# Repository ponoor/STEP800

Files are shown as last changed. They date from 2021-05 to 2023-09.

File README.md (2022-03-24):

# STEP800
8-axis stepper motor driver for Open Sound Control

step800_r1_1

STEP800 is a 8-axis stepper motor driver designed for art or design projects. STEP800 combines the following elements into one single board:

- [Arduino Zero](https://www.arduino.cc/en/Guide/ArduinoZero)
- Ethernet shield
- 8 stepper motor drivers
- Sensor inputs for homing

The current firmware is focused on working with [Open Sound Control](http://opensoundcontrol.org/) (OSC) via Ethernet, which is a common protocol for creative coding environments, like openFrameworks, Processing, Max, Unity, or Touch Designer.

Stepper driver chips are STMicroelectronics's [L6470](https://www.st.com/en/motor-drivers/l6470.html) which provide most of functionalities as a stepper driver.

Friend of STEP800 : [STEP400](https://github.com/ponoor/STEP400)

## Store
https://ponoor.com/en/shop/

## Documentation
https://ponoor.com/en/docs/step-series/

Forum: https://github.com/ponoor/step-series-support/discussions

## Repository Contents
### Firmware

**Important Note:**
The latest firmware is available at [STEP-series Universal Firmware](https://github.com/ponoor/step-series-universal-firmware) repository. Following directories and Releases are not maintained anymore. 

These 2 folders contain same codes.
- [/STEP800_firmware](https://github.com/ponoor/STEP800/tree/main/STEP800_firmware) : Arduino Sketch folder
- [/firmware-platformIO/STEP800_firmware](https://github.com/ponoor/STEP800/tree/main/firmware-platformIO/STEP800_firmware) : PlatformIO folder

### Hardware
[/hardware](https://github.com/ponoor/STEP800/tree/main/hardware) : Eagle design files, BOM lists, and a schematics PDF

### Others
[/configTool](https://github.com/ponoor/STEP800/tree/main/configTool) : The configuration tool consists of a html and JavaScritpts.

## Firmware dependency
- **[OSC Library](https://github.com/CNMAT/OSC)** from CNMAT
- **[Ponoor L6470 Library](https://github.com/ponoor/Ponoor_L6470_Library)**
- **[ArduinoJSON Library](https://arduinojson.org/)**
- **[Adafruit SleepyDog Arduino Library](https://github.com/adafruit/Adafruit_SleepyDog)**

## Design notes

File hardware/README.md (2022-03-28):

# Diagram
```mermaid
flowchart LR
	MCU ---|SPI/SERCOM4| W5500 --- Ethernet
	MCU --- |SPI/SERCOM3|L6470 --> Motor
  MCU --> |SPI/SERCOM2|74HC165 --> 74HC595 --> MCU
	HomeSw -->|SW| L6470
	DIPSW --> 74HC165
	74HC595 --> Brake
  ```
  
  Check the [document](https://ponoor.com/en/docs/step-series/technical-information/hardware-step800/) for details.

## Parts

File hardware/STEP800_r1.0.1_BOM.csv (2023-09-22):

# | Name | Value | Description | Package | Manufacture | MPN | Qty | Parts | Type | SMT | THT | BGA/QFP
1 | SMD-LED | GREEN | Various green LEDs | LED-0603 | Everlight Elec | 19-213/GHC-YR1S2M/3T | 9 | 3.3V, BUSY1, BUSY2, BUSY3, BUSY4, BUSY5, BUSY6, BUSY7, BUSY8 | SMT | 9
2 | MLCC | 100nF / 25V | 100nF / 20% / 25V / X5R | C0402 | Samsung Electro-Mechanics | CL05A104KA5NNNC | 32 | C1, C3, C7, C8, C9, C10, C12, C13, C14, C15, C16, C17, C20, C21, C24, C31, C32, C33, C34, C35, C44, C45, C46, C47, C72, C73, C74, C75, C84, C85, C86, C87 | SMT | 32
3 | MLCC | 10uF/10V | 10uF / 20% / 10V / X5R | C0805 | Samsung Electro-Mechanics | CL21A106KOQNNNG | 9 | C11, C36, C37, C38, C39, C76, C77, C78, C79 | SMT | 9
4 | MLCC | 47uF/6.3V | 47uF / 20% / 6.3V / X5R | C1206 | Samsung Electro-Mechanics | CL31A476MQHNNNE | 2 | C18, C19 | SMT | 2
5 | MLCC | 10uF/50V | 10uF / 20% / 50V / X5R | C1206 | Samsung Electro-Mechanics | CL31A106KBHNNNE | 2 | C2, C6 | SMT | 2
6 | MLCC | 4.7uF / 6.3V | 4.7uF / 20% / 6.3V / X5R | C0603 | Samsung Electro-Mechanics | CL10A475KQ8NNNC | 1 | C22 | SMT | 1
7 | MLCC | 10nF/50V | 10nF / 20% / 50V / X5R | C0603 | Samsung Electro-Mechanics | CL10B103KB8NNNC | 10 | C23, C28, C40, C41, C42, C43, C80, C81, C82, C83 | SMT | 10
8 | MLCC | 22nF 50V | 22nF / 20% / 50V / X5R | C0402 | Walsin Tech Corp | 0402F223Z500CT | 1 | C27 | SMT | 1
9 | MLCC | 6.8nF/25V | 6.8nF / 20% / 25V / X5R | C0402 | Murata Electronics | GCM155R71E682KA37D | 2 | C29, C30 | SMT | 2
10 | MLCC | 22pF/50V | 22pF / 10% / 50V / X5R | C0402 | YAGEO | CC0402JRNPO9BN220 | 4 | C4, C5, C25, C26 | SMT | 4
11 | MLCC | 220nF / 25V | 220nF / 20% / 25V / X5R | C0603 | Samsung Electro-Mechanics | CL10F224ZA8NNNC | 8 | C65, C67, C69, C71, C105, C107, C109, C111 | SMT | 8
12 | Chemical Capacitor | 220uF / 50V | 220uF �}20% 50V 10mm | SMD,10x10mm | Rubycon | 50TZV220M10X10.5 | 8 | C48, C49, C50, C51, C88, C89, C90, C91 | SMT | 8
13 | MLCC | 100nF/50V | 100nF / 20% / 50V / X5R | C0603 | Walsin Tech Corp | 0603B104K500CT | 32 | C52, C53, C54, C55, C56, C57, C58, C59, C60, C61, C62, C63, C64, C66, C68, C70, C92, C93, C94, C95, C96, C97, C98, C99, C100, C101, C102, C103, C104, C106, C108, C110 | SMT | 32
14 | Shrouded header | 2.5mm, 4P | B4B-XASK-1 | B4B-XASK-1 | JST | B04B-XASK-1(LF)(SN) | 8 | CN1, CN2, CN3, CN4, CN9, CN10, CN11, CN12 | NO MOUNT
15 | Shrouded header | 2.5mm, 3P | B3B-XASK-1 | B3B-XASK-1 | JST | B03B-XASK-1(LF)(SN) | 8 | CN5, CN6, CN7, CN8, CN13, CN14, CN15, CN16 | THT | 8
16 | Switching diode array | BAV99 | Series-pair diode array | SOT23-3 | Nexperia | BAV99,215 | 8 | D14, D15, D16, D17, D26, D27, D28, D29 | SMT | 8
17 | Zener Diode | 5.6V, 300mW | 5.6V �}7% 300mW | SOD-323 | CBI | MM3Z5V6 | 1 | D4 | SMT | 1
18 | SMD-LED | Red | general LED red | LED-0603 | Lite-On | LTST-C193KRKT-5A | 9 | FLAG1, FLAG2, FLAG3, FLAG4, FLAG5, FLAG6, FLAG7, FLAG8, TX | SMT | 9
19 | Ethernet Controller |  |  | TQFP48 | WIZnet | W5500 | 1 | IC1 | SMT | 1 |  | 1
20 | DIP Switch |  | 8 digits | 2.54mm pitch SMD | kangshen | DSIC08LSGET | 1 | ID | SMT | 1
21 | DC Power receptacle |  | DC Power Receptacle Jack 5A 2.0mm 6.2mm | POWERJACK_SLOT | XKB Connectivity | DC-005-5A-2.0 | 1 | J1 | THT |  | 1
22 | Box header |  | Header 10P 0.100"(2.54mm) 2 | 61201021621 | BOOMELE(Boom Precision Elec) | C5665 | 1 | J2 | THT |  | 1
23 | Micro SD card slot |  |  |  | XUNPU | TF-115K | 1 | J4 | SMT | 1
24 | 3.81mm 4pin header |  |  |  | Ningbo Kangnex Elec | WJ15EDGVC-3.81-4P | 8 | J5, J6, J7, J8, J9, J10, J11, J12 | THT |  | 8
25 | SMD-LED | Orange | general LED orange | LED-0603 | Lite-On | LTST-C191KFKT | 1 | L | SMT | 1
26 | Ferrite Beads | 330R-1500MA | 330ƒ¶ @ 100MHz 1.5A | L0805 | Murata Electronics | BLM21PG331SN1D | 2 | L1, L2 | SMT | 2
27 | DC-DC Converter | P78E05-1000 | 9-36V input, 5V output, 1000mA | CONV_P78E05-1000 | CUI Inc. | P78E05-1000 | 1 | PS1 | THT |  | 1
28 | P-MOSFET |  | 60V 50A | D-PAK(TO252) | VBsemi Elec | STD35P6LLF6-VB | 1 | Q1 | SMT | 1
29 | Crystal Resonators | 32.768kHz | CRYSTAL | SMD-3215_2P | Seiko | SC-32S32.768kHz20PPM6pF | 1 | Q2 | SMT | 1
30 | Crystal Oscillator |  | 16MHz �}100ppm 3.3V | SMD5032-4P | Shenzhen SCTF Elec | S5D16.000000B20F30T | 1 | Q3 | SMT | 1
31 | Chip Resistor | 5.1k | �}0.5% 0.1W | R0603 | YAGEO | RC0603FR-075K1L | 2 | R1, R2 | SMT | 2
32 | Chip Resistor | 1M 1/10W | 5% 1/10W | R0603 | YAGEO | AC0603JR-071ML | 1 | R10 | SMT | 1
33 | Chip Resistor | 10R | 5% 1/10W | R0603 | YAGEO | RC0603JR-0710RL | 1 | R11 | SMT | 1
34 | Chip Resistor | 330R | 5% 1/10W | R0603 | YAGEO | RC0603JR-07330RL | 3 | R12, R13, R22 | SMT | 3
35 | Chip Resistor | 100R | 5% 1/10W | R0603 | YAGEO | RC0603JR-07100RL | 8 | R14, R15, R16, R17, R18, R19, R20, R21 | SMT | 8
36 | Chip Resistor | 100k | 5% 1/10W | R0603 | YAGEO | RC0603JR-07100KL | 4 | R3, R4, R5, R9 | SMT | 4
37 | Chip Resistor | 12.4K | 1�“ 1/10W | R0603 | YAGEO | AC0603FR-0712K4L | 1 | R8 | SMT | 1
38 | Tactile Switch |  | SWITCH-SPST | 4.6x3.2 | ALPS Electric | SKRPABE010 | 1 | RESET | SMT | 1
39 | Array Chip Resistor | 100k | 5% 1/16W | R0603 x4 | Bourns | CAY16-104J4LF | 2 | RN1, RN2 | SMT | 2
40 | Array Chip Resistor | 330 | 5% 1/16W | R0603 x4 | Bourns | CAY16-331J4LF | 5 | RN3, RN6, RN7, RN8, RN9 | SMT | 5
41 | Array Chip Resistor | 33 | 5% 1/16W | R0603 x4 | Bourns | CAY16-330J4LF | 1 | RN4 | SMT | 1
42 | Array Chip Resistor | 49.9 | 1% 1/16W | R0603 x4 | Bourns | CAY16-49R9F4LF | 1 | RN5 | SMT | 1
43 | SMD-LED | Yellow | general LED yellow | LED-0603 | Lite-On | LTST-C191KSKT | 1 | RX | SMT | 1
44 | Pin Header | 10 pin | Cortex Debug Connector | 1.27mm Pin Header 10P | Amphenol ICC | 20021121-00010C4LF | 1 | SWD | SMT | 1
45 | Logic IC | 74HC165PW | 8-bit parallel-in/serial out shift register | TSSOP16 | Nexperia | 74HC165PW,118 | 1 | U1 | SMT | 1 |  | 1
46 | TVS Diode Array | USBLC6-2SC6 | STMicroelectronics USBLC6 | SOT23-6L | UMW | USBLC6-2SC6 | 1 | U2 | SMT | 1
47 | Logic IC | 74HC595 | 8-Bit Shift Register (Serial to Parallel) | TSSOP16 | Nexperia | 74HC595PW,118 | 1 | U3 | SMT | 1 |  | 1
48 | Voltage Regulator | LD1117S33 | 3.3V 0.8A | SOT223 | STMicroelectronics | LD1117S33TR | 1 | U4 | SMT | 1
49 | MCU |  |  | TQFP-48 | Microchip | ATSAMD21G18A-AU | 1 | U5 | SMT | 1 |  | 1
50 | Stepper Driver IC |  |  | HTSSOP28 | STMicroelectronics | L6470HTR | 8 | U6, U7, U8, U9, U10, U11, U12, U13 | SMT | 8 |  | 8
51 | USB Type C Connector |  | USB - Type C Female 16 SMT | USB-C_USB2.0-TYPE-C | XKB Connectivity | U262-161N-4BVC11 | 1 | USB1 | THT |  | 1
52 | Barrier Terminal Block | 7.62mm, 2P |  | 7.62mm | Ningbo Kangnex Elec | WJ25C-B-7.62-2P | 1 | X1 | THT |  | 1
53 | Crystal Resonators | 25MHz | 25MHz �}20ppm12pF | CRYSTAL-3225 | Yangxing Tech | X322525MOB4SI | 1 | X2 | SMT | 1
54 | RJ45 Jack with Magnetics |  |  |  | Hanrun | HR871181A | 1 | X3 | THT |  | 1
 |  |  |  |  |  |  |  |  |  | 201 | 14 | 12

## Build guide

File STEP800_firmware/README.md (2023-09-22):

<strong>This directory is not up to date, and not maintained any more.</strong>

Please visit STEP-series Universal Firmware repository for the latest firmware.<br />
https://github.com/ponoor/step-series-universal-firmware

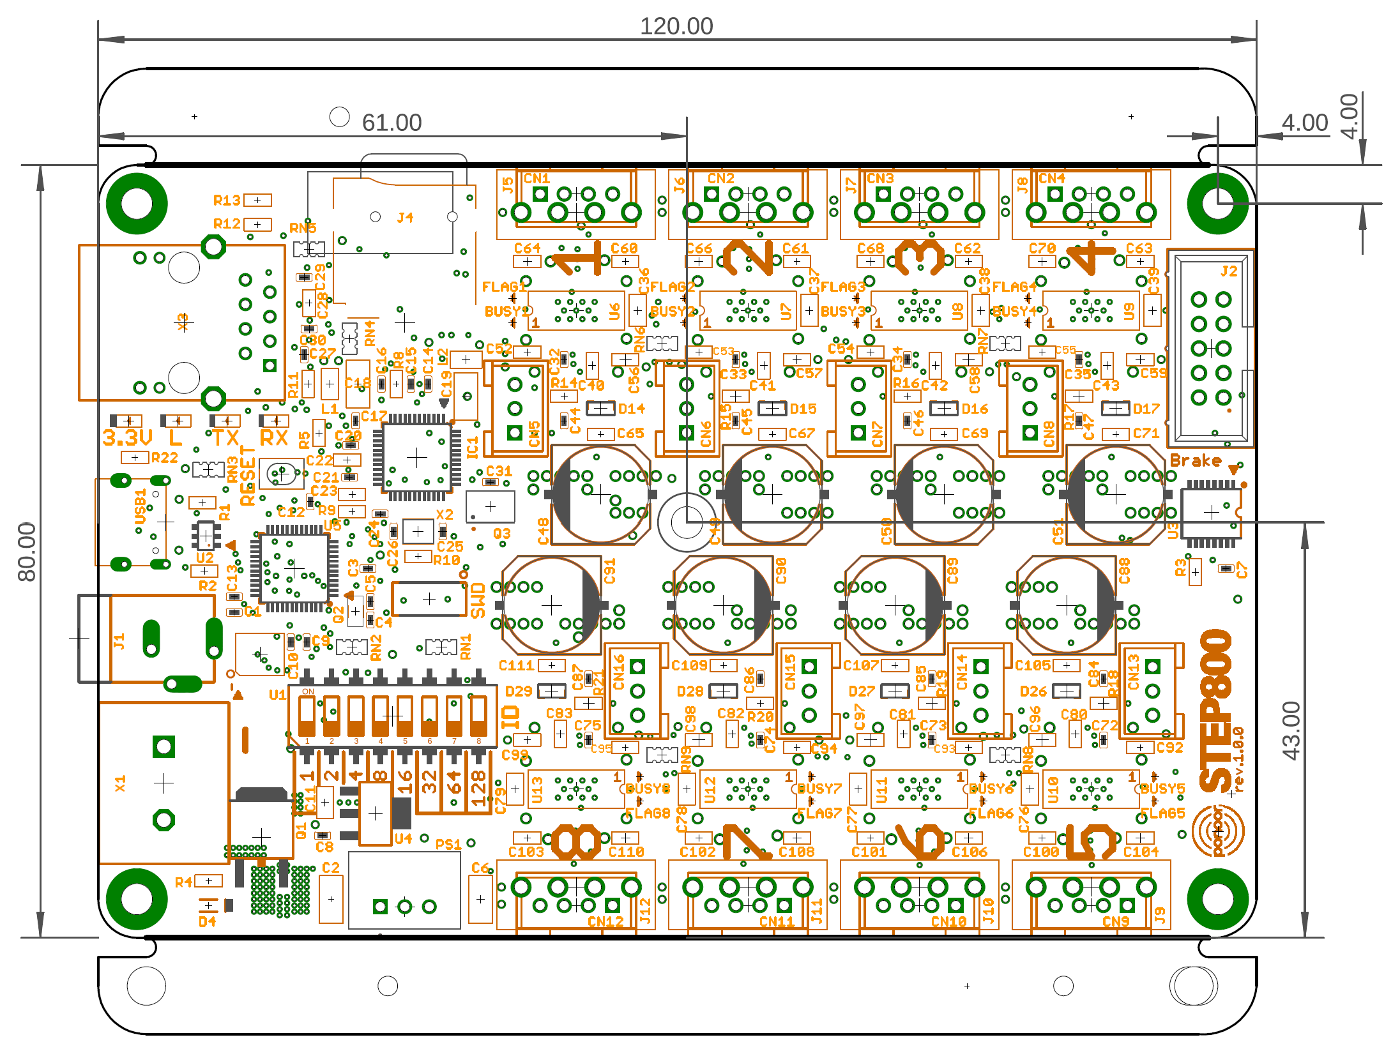
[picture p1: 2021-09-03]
hardware/step800_r1_0_0_dimension.png

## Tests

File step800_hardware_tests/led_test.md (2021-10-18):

# STEP800 LED test
## Preparation
### Connection
- Connect STEP800 to PC with an USB-C to Type-A cable
- Give a 24V power supply to STEP800

### Upload the test program
1. Download the test program from [here](https://github.com/ponoor/STEP800/tree/develop/step800_hardware_tests/step800_led_test), or unizip the attached file. 
2. Open the `step800_led_test.ino` with Arduino IDE.
3. Specify the IDE's target board as Arduino Zero (Native USB Port).


4. Click to the "Tools" menu and then *Port*. Then you should be able to find a serial port(s) and select one with information as `Arduino Zero (Native USB Port))` .


5. Click the upload button. The compile process will take a while.
6. After the compile process is done, Arduino IDE will start upload it to STEP800. You will see the `TX` and `RX` LEDs on STEP800 are blinking during the upload process.
7. If the uploading process is done without problems, you will see the `L` led is turned on.

## Test
### Open the Serial Monitor
Click the lens button on the top right corner of the IDE window.


Then you will see a new Serial Monitor window. You will find some settings in the bottom of the window but you can leave them as defaults.

### FLAG LEDs test
Select a transmission text form (see below) and type `f`  then return key.
This command turn all FLAG LEDs on.


### BUSY LEDs test
Type `b` + return key should cause turning all BUSY LEDs on.

### Clear LEDs
Type `c` + return key will turn all LEDs off.

---

rev 2021-09-13-01, by kanta

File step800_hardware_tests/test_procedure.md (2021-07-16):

## Preparation
### Required tools
- PC which installed Arduino IDE software
- Atmel-ICE Basic https://www.microchip.com/DevelopmentTools/ProductDetails/ATATMEL-ICE
- Power Supply DC jack 24V 1A
- microSD or microSDHC card
- USB Type-C to Type-A cable
- Power Supply 24V 1A, with DC plug 5.5mm outer diameter, 2.1mm inter diameter, center plus
- Network Switch which support 100BASE-TX or faster.
- Ethernet cable CAT5 or higher.

### microSD card setup
1. Format the **microSD** or **microSDHC** card with FAT16 or FAT32.
    Note : microSDXC card will not work.
2. Download the test text data from [here](https://raw.githubusercontent.com/kanta/STEP400_prototype/master/rev4/configTool/sample-setups/SM-42BYG011_24V/config.txt).
3. Copy it to the top directory of the microSD card.
4. Remove the card from a PC and put into the microSD card slot on STEP800.

### Arduino IDE setup
1. Download and install latest Arduino IDE from https://www.arduino.cc/en/Main/Software
2. Install SAMD boards core. Procedure is explained here: https://www.arduino.cc/en/Guide/ArduinoZero
3. Specify the target board as `Arduino Zero (Native USB Port)`.


#### Install Arduino Libraries for the test program

1. Open the IDE and click to the "Sketch" menu and then *Include Library*  > *Manage Libraries*.
2. Type "ponoor" to the search box located on the top right of the window. 


3. You should be able to find "Ponoor L6470 Library". Select it and click the *Install* button.
4. Then install one another library “FlashStorage”. The procedure is same as above.

#### Download and Compile the test program

1. Download the program from [here](https://github.com/ponoor/STEP800/blob/main/step800_hardware_tests/Arduino/step800_hardware_tests/step800_hardware_tests.ino), and open it with the Arduino IDE software.
2. Specify the target board as `Arduino Zero (Native USB Port)` .

3. Press the “VERIFY” button. Then Arduino IDE starts the compile the program (which called “Sketch” in the IDE).



4. If the compiling process is done successfully, you will see a “Done compiling.” sign.


## Programming the MCU
### 1. Apply the power supply
- Apply 24V DC to the PCB with DC input jack (5.5mm outer diameter, 2.1mm inter diameter, center plus). 
[ ] Check the green LED (designator `3.3V` )
### 2. Connect Atmel-ICE Basic
- Connect Atmel-ICE Basic with a PC with USB microB cable.
- Connect the programming cable to the “**SAM**” connector of the Atmel-ICE Basic
- For the cable, use the right connector in the following photo to the Atmel-ICE Basic, and the center connector to the PCB.  We won’t use the left connector.


- Remove the small plastic cover from `SWD` pin header on the PCB. Do not discard this cover, we will put this back to the connector later.
- Then connect a programming socket (the 1.27mm pitch 10pin connector in the middle of the cable) to `SWD` pinheader on the PCB. Be aware of the small circle marking which placed the pin no.1 of the `SWD` connector. The red line of the programming cable indicates the pin no.1 side of the programming header.


- [ ] Green LED on Atmel-ICE Basic should be on.

### 3. Burn Arduino bootloader to the PCB
- Arduino bootloader can write from Arduino IDE. Select `Programmer` item from `Tools` menu,  then select `Atmel-ICE`.
    


- Then select `Burn Bootloader` item of `Tools` menu. 
    


- After programming process,
- [ ] Orange LED on the PCB (designator `L` ) will be fading in & out slowly.

### 4. Put the cover back to the SWD connector
Remove Atmel-ICE-Basic from the PCB and put the black plastic cover back to the SWD connector.

## Upload the test program
### Select a serial port from Arduino IDE
1. Connect the USB connector to a PC with an USB type-C cable. 
2. Open the IDE and click to the "Tools" menu and then *Port.* Then you should be able to find a serial port(s) and select one with information as `Arduino Zero (Native USB Port))` .

3. If there is no serial port in the menu, probably the Arduino Zero bootloader isn’t programmed correctly. 
4. Click the upload button. The compile process will take a while. 
5. After the compile process is done, Arduino IDE will start upload it to STEP800. You will see the `TX` and `RX` LEDs on STEP800 are blinking during the upload process.

## Setups for the test
### Select the serial port again
Once the first sketch is uploaded to STEP800, the name of serial port will change from the original one. Select one with information as `Arduino Zero (Native USB Port))` again.

### Connect the Ethernet connector
Connect the Ethernet connector to a network switch with an Ethernet cable. This is used for check the ethernet link connection is established or not. 

## Test Procedure
Finally we are ready to start the test!

### Open a Serial Monitor
Click the lens button on the top right corner of the IDE window.


Then you will see a new Serial Monitor window. You will find some settings in the bottom of the window but you can leave them as defaults.

### Send a test command
Select a transmission text form (see below) and type `t`  then return key.


## Description of each tests
### microSD card slot

**Description**
This test checks the microSD card slot is working correctly or not.
The successful test result will look like this;

     -------------- SD card -------------- 
    SD card initialize: Ok
    SD_DETECT_PIN: 0 Ok
    
    Test result: Passed

**SD card initialize**
This item checks the connection with microSD card. If this test failed, please check followings;

- The microSD card is inserted
- Using a microSD or a microSDHC card, NOT microSDXC
- The microSD card is formatted with FAT16 or FAT32 formant, NOT exFAT 
- SPI wires for the microSD slot are wired correctly. 

**SD_DETECT_PIN**
This items checks the logical correctness of the microSD card detect pin.

**Related pins**

| MCU pin# | Function |
| --- | --- |
| 13 | microSD SPI CS |
| 19 | microSD SPI MOSI (Shared with W5500) |
| 20 | microSD SPI SCK (Shared with W5500)  |
| 21 | microSD SPI MISO (Shared with W5500) |
| 10 | SD_DETECT_PIN |

### Auxiliary Pins

**Descriptions**
This test checks the auxiliary pad pins which exposed in the bottom side of the PCB.
The successful test result will look like this;

     -------------- Auxiliary Pins --------------
    Auxiliary Pins connection state: Ok
    
    Test result: Passed

This test confirms that each pin is not interfering with each other.

**Related pins**

| MCU pin# | Pad name (in Bottom side) |
| --- | --- |
| 31 | SDA |
| 32 | SCL |
| 22 | D38 |
|12|D9|
|11|D8|
|7|A1|
|15|D1|
|30|D7|

### Ethernet

**Descriptions**
This test the Ethernet controller chip and a physical connection of the network.
The successful test result will look like this;

     -------------- Ethernet --------------
    Ethernet hardware status: 3, -EthernetW5500 Ok
    Ethernet link status: 2 ..Ok
    
    Test result: Passed

**Ethernet hardware status**
This test checks the SPI communication with the Ethernet controller chip W5500 (`IC1`). If this test failed, please check the W5500 chip or wiring.

**Ethernet link status**
This test checks the physical connection of Ethernet. This test wait a few seconds to establish the connection. If the connection couldn’t establish within the waiting period, the test becomes failed. If so, please check the followings;

- Ethernet cable is connected with a network switch.
- Check the RJ45 connector `X3` and related components include; `C34, C35, C36, C37, R14, RN2, RN3`

**Related pins**

| MCU pin# | Function |
| --- | --- |
| 9 | W5500 RESET |
| 27 | W5500 SPI CS |
| 19 | W5500 SPI MOSI (shared with microSD) |
| 20 | W5500 SPI SCK (shared with microSD)  |
| 21 | W5500 SPI MISO (shared with microSD) |

### L6470

**Description**
This test checks the motor driver chip L6470. 
The successful test result will look like this;

```
-------------- L6470 --------------     
L6470 SPI connection: Ok
L6470 ID#1
 STATUS: 0x7E30  Ok
 SW_F: 0 Ok
 BUSY: 0 Ok
L6470 ID#2
 STATUS: 0x7E30  Ok
 SW_F: 0 Ok
 BUSY: 0 Ok
L6470 ID#3
 STATUS: 0x7E30  Ok
 SW_F: 0 Ok
 BUSY: 0 Ok
L6470 ID#4
 STATUS: 0x7E30  Ok
 SW_F: 0 Ok
 BUSY: 0 Ok
L6470 ID#5
 STATUS: 0x7E30  Ok
 SW_F: 0 Ok
 BUSY: 0 Ok
L6470 ID#6
 STATUS: 0x7E30  Ok
 SW_F: 0 Ok
 BUSY: 0 Ok
L6470 ID#7
 STATUS: 0x7E30  Ok
 SW_F: 0 Ok
 BUSY: 0 Ok
L6470 ID#8
 STATUS: 0x7E30  Ok
 SW_F: 0 Ok
 BUSY: 0 Ok

Test result: Passed
```

**L6470 SPI connection**
This results shows the physical connection of the SPI daisy chain of 8 L6470s are working or not. All SPI pins of all L6470s and the MCU have to be connected properly to establish the SPI communication.
If this test failed, please check the connections of following pins;

| MCU pin# | L6470 pin# | Function |
| --- | --- | --- |
| 3 | 23 | L6470 SPI CS |
| 8 | 3 | L6470 RESET |
| 25 | 20 | L6470 SPI MOSI |
| 28 | 19 | L6470 SPI SCK  |
| 29 | 18 | L6470 SPI MISO |

**STATUS**
This item shows the status of each PowerSTEP01. There are several possible errors here.

- `OCD(Over Current) detected.` : This error indicates an overcurrent detection event. Probably something is wrong in following pins;

| L6470 pin# | Function |
| --- | --- |
| 1 | OUT1A |
| 14 | OUT1B |
| 15 | OUT2A |
| 28 | OUT2B |

- `UVLO(Under Voltage Lock Out) detected.`  : This error will happen then a VCC of the L6470 is too low.  Check the power supply is connected properly, and following pin connections;

| L6470 pin# | Function |
| --- | --- |
| 2, 26 | VSA |
| 12, 16 | VSB |
| 10 | CP |
| 11 | VBOOT |

- `OCD+UVLO detected.` : This error happens when the external clock source is not provided. Check the crystal oscillator `Q3` and external clock input and output pins of L6470. The external clock is daisy chained among L6470s, `Q3` → `U6` → `U7` → `U8` → `U9` → `U10` → `U11` → `U12` → `U13`.

| L6470 pin# | Function |
| --- | --- |
| 7 | OSCIN |
| 8 | OSCOUT |

**SW_F**
This item checks the state of SW pin of PowerSTEP01, which connected to HOME sensor connector. 

| L6470 pin# | Function |
| --- | --- |
| 4 | SW |

### DIP Switch

**Descriptions**
This test checks the DIP switch (designator `ID`) and you need to move all digits of the switch by yourself to complete the test.
Initially you will see the following message.

```
-------------- DIP Switch --------------
Turn the digit #1 ON...
```
Move the specified digit of the switch. Then you will see a next message.
Eventually the test result will look something like this;

```
-------------- DIP Switch --------------
Turn the digit #1 ON....Done.
Turn the digit #1 OFF...Done.
Turn the digit #2 ON.Done.   
Turn the digit #2 OFF..Done.
Turn the digit #3 ON..Done. 
Turn the digit #3 OFF..Done.
Turn the digit #4 ON..Done. 
Turn the digit #4 OFF..Done.
Turn the digit #5 ON..Done. 
Turn the digit #5 OFF.Done.
Turn the digit #6 ON..Done.
Turn the digit #6 OFF..Done.
Turn the digit #7 ON...Done.
Turn the digit #7 OFF.Done. 
Turn the digit #8 ON..Done.
Turn the digit #8 OFF..Done.

Test result: Passed
```

You will see the message every time you moved the digit.
This test will be finished when all 8 digits are successfully moved.

If you need to cancel this DIP switch test you can type `b`.

### Test result

Finally you will see the result. The last line shows the total result.

```
-------------- Result of Hardware Test --------------
SD Card: Ok
Auxiliary Pins: Ok
Ethernet: Ok
L6470: Ok
DIP switch: Ok

Test result: Passed
```

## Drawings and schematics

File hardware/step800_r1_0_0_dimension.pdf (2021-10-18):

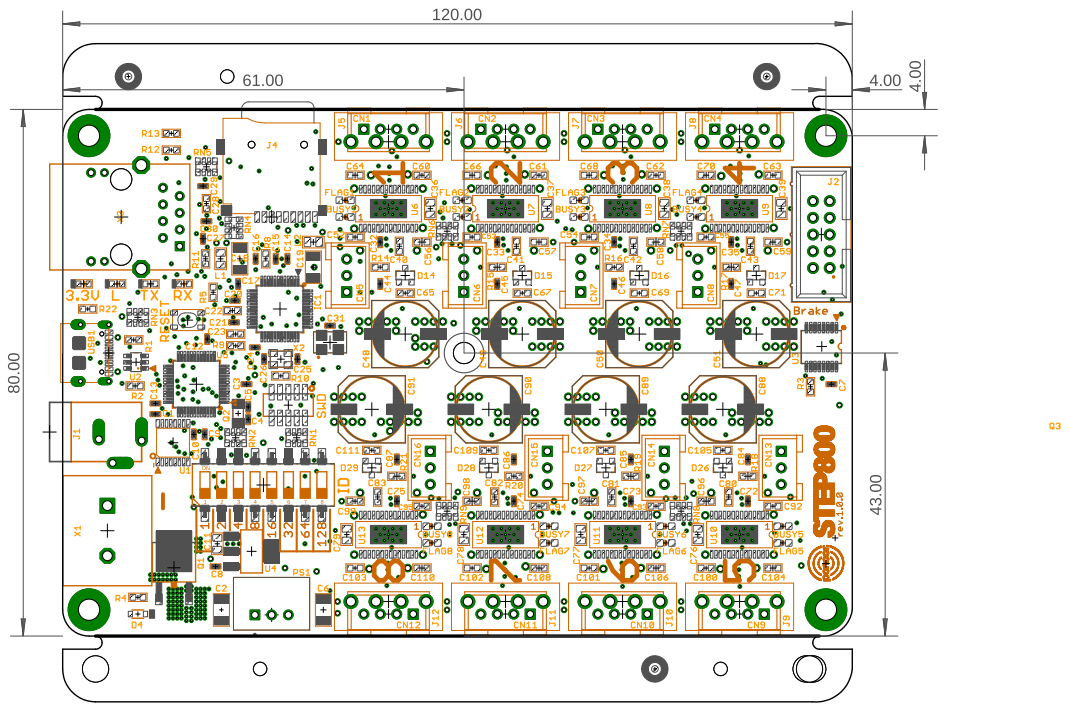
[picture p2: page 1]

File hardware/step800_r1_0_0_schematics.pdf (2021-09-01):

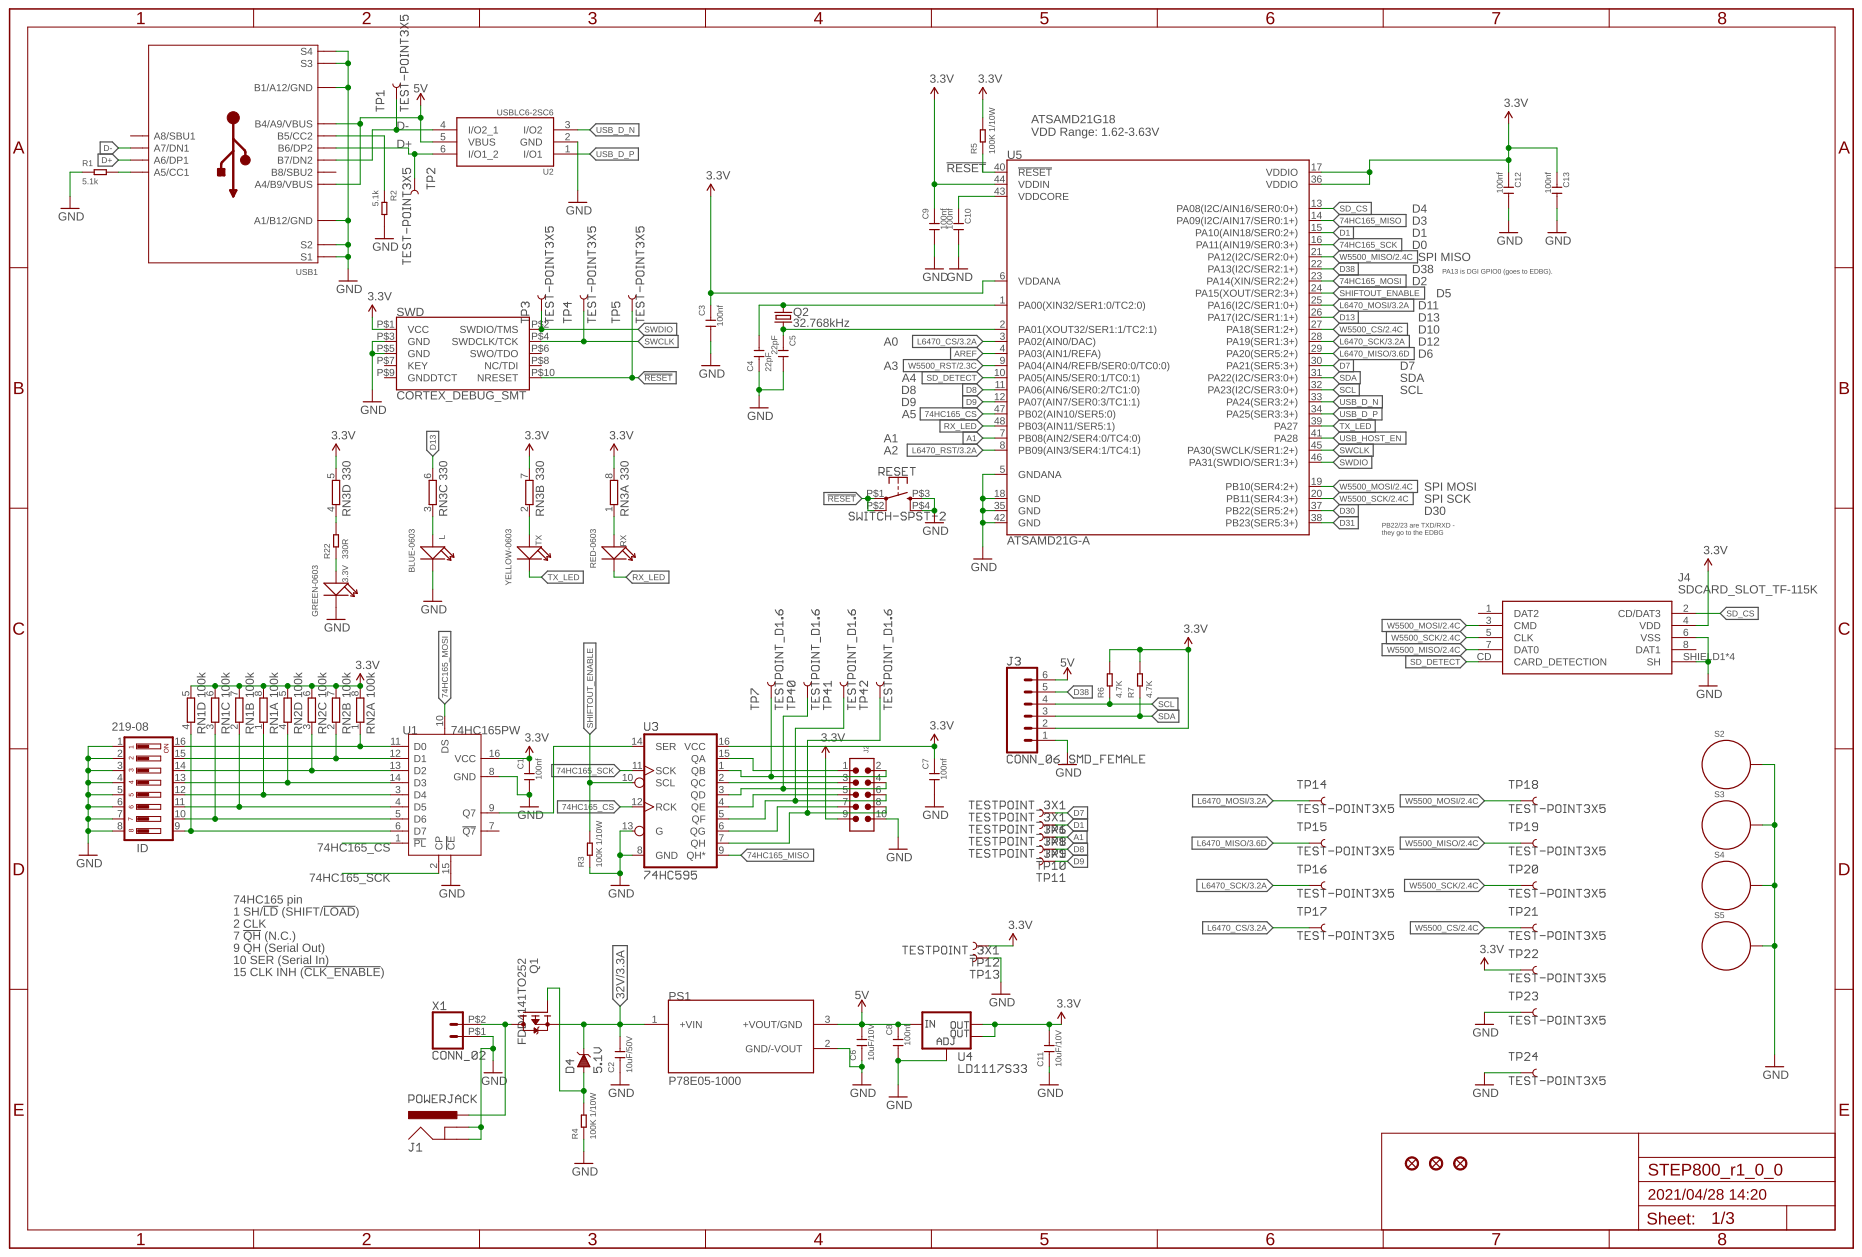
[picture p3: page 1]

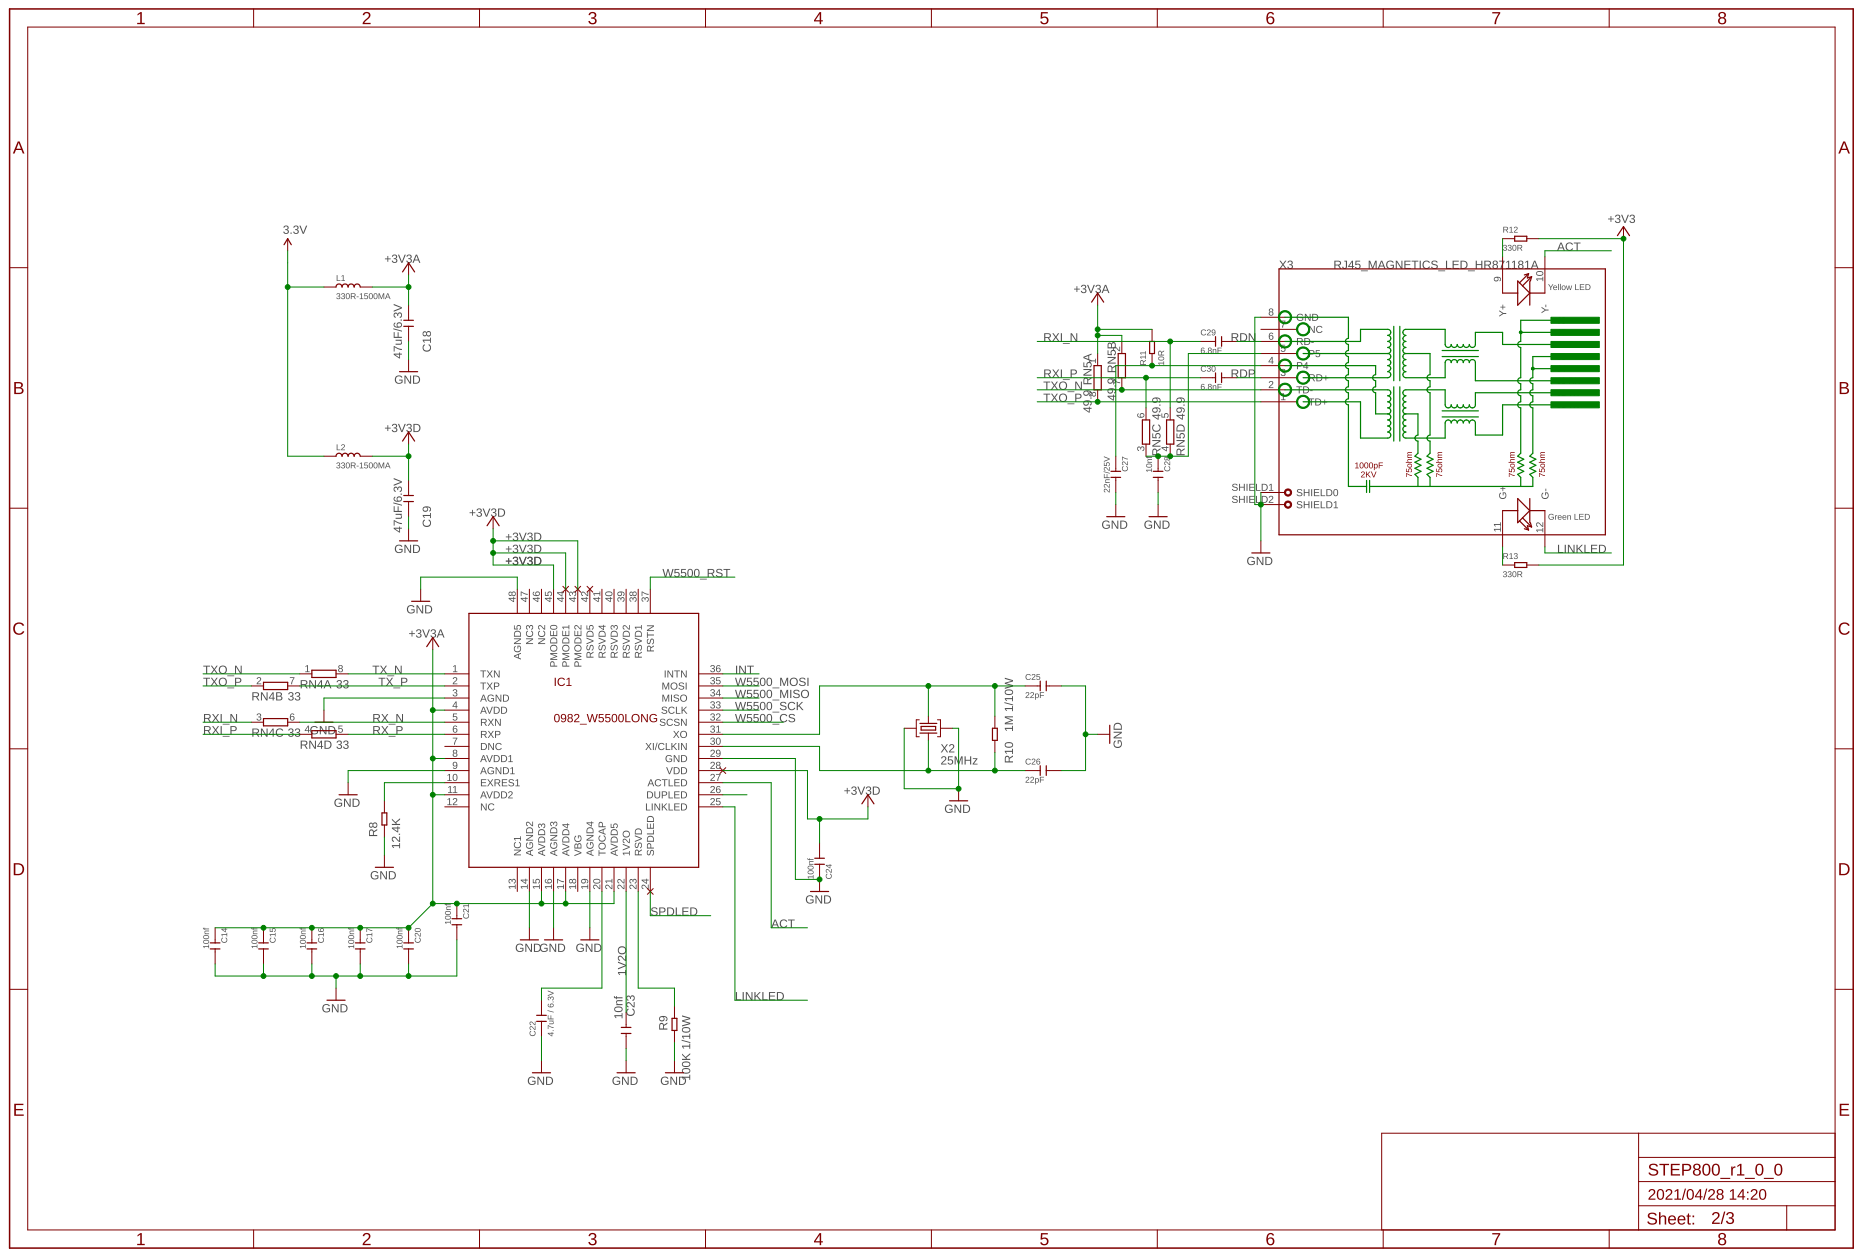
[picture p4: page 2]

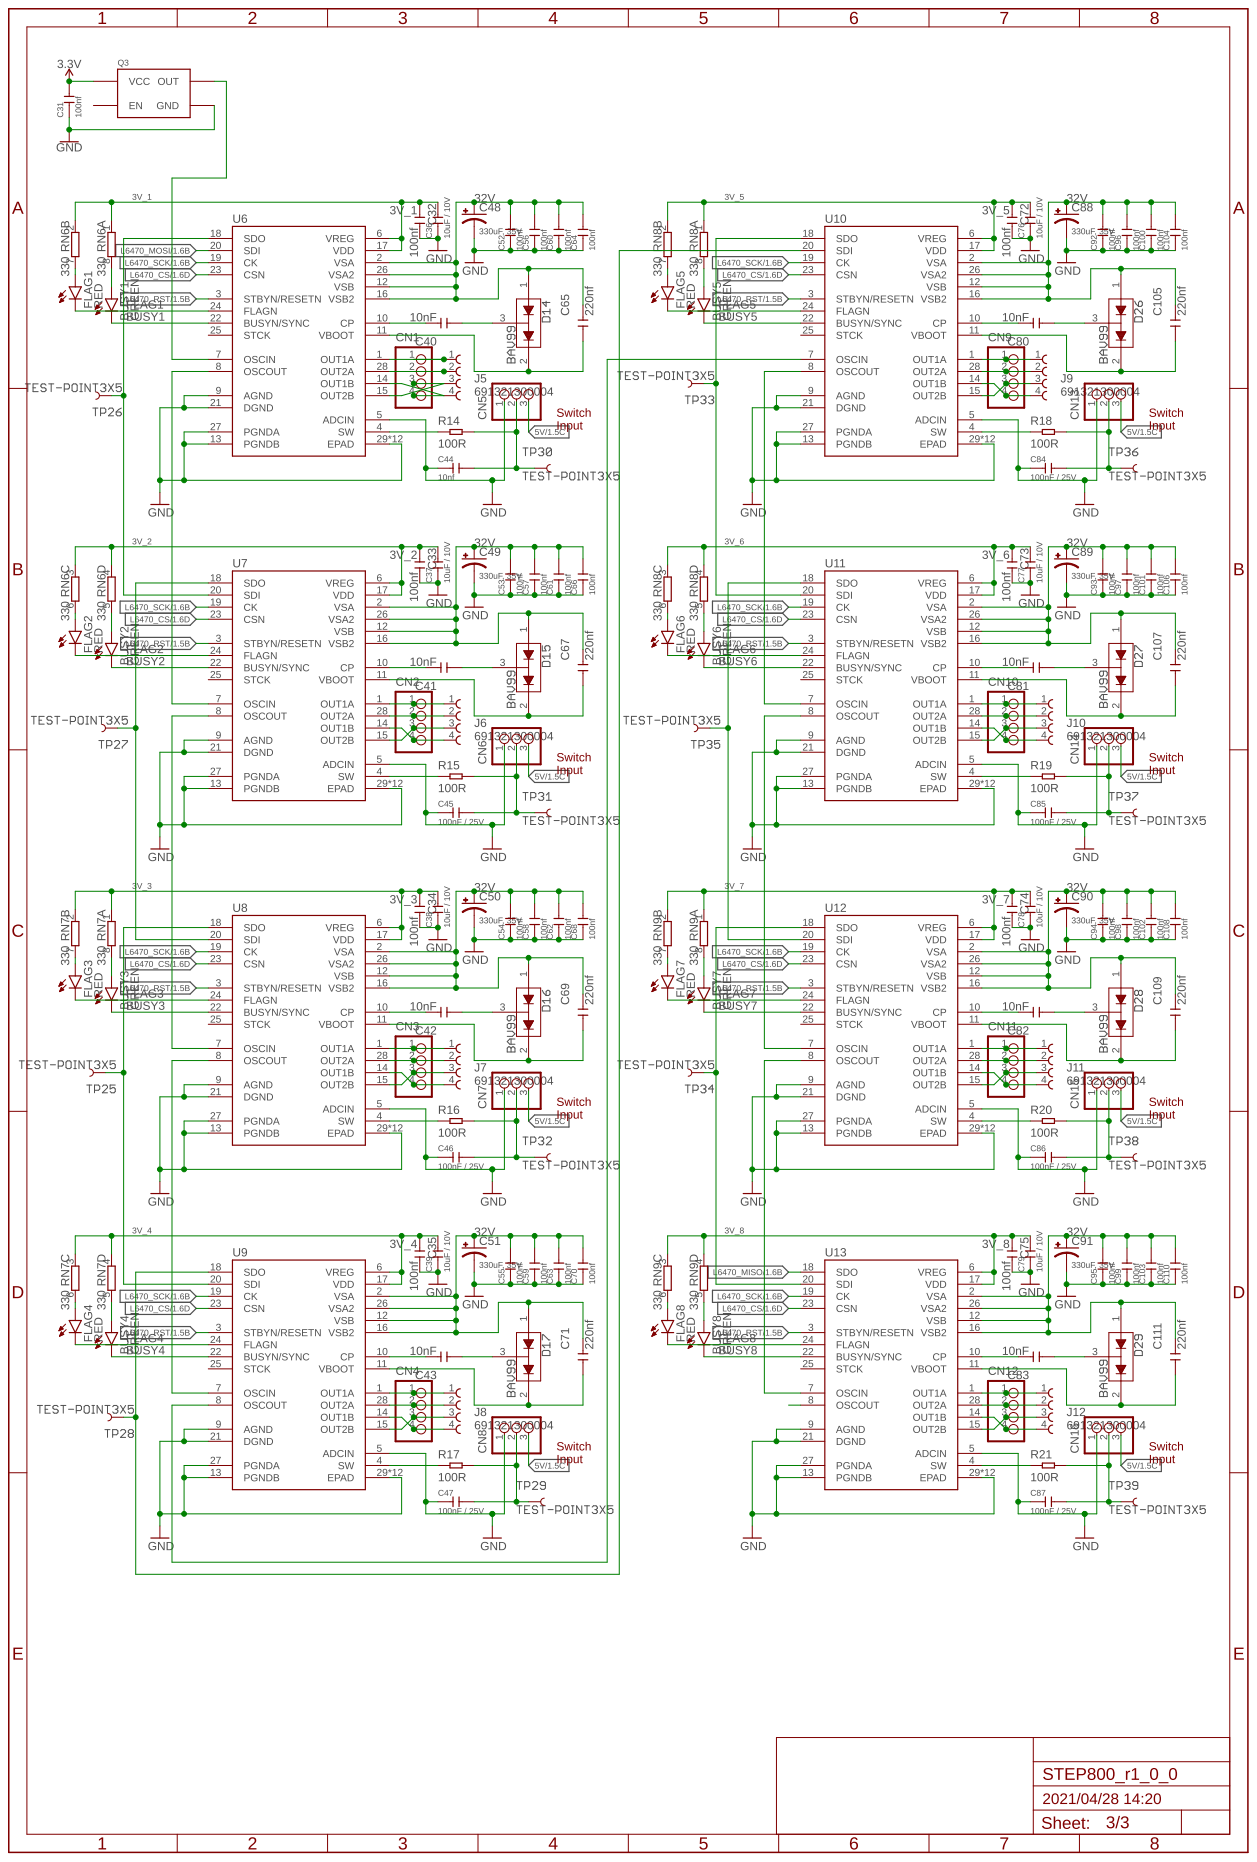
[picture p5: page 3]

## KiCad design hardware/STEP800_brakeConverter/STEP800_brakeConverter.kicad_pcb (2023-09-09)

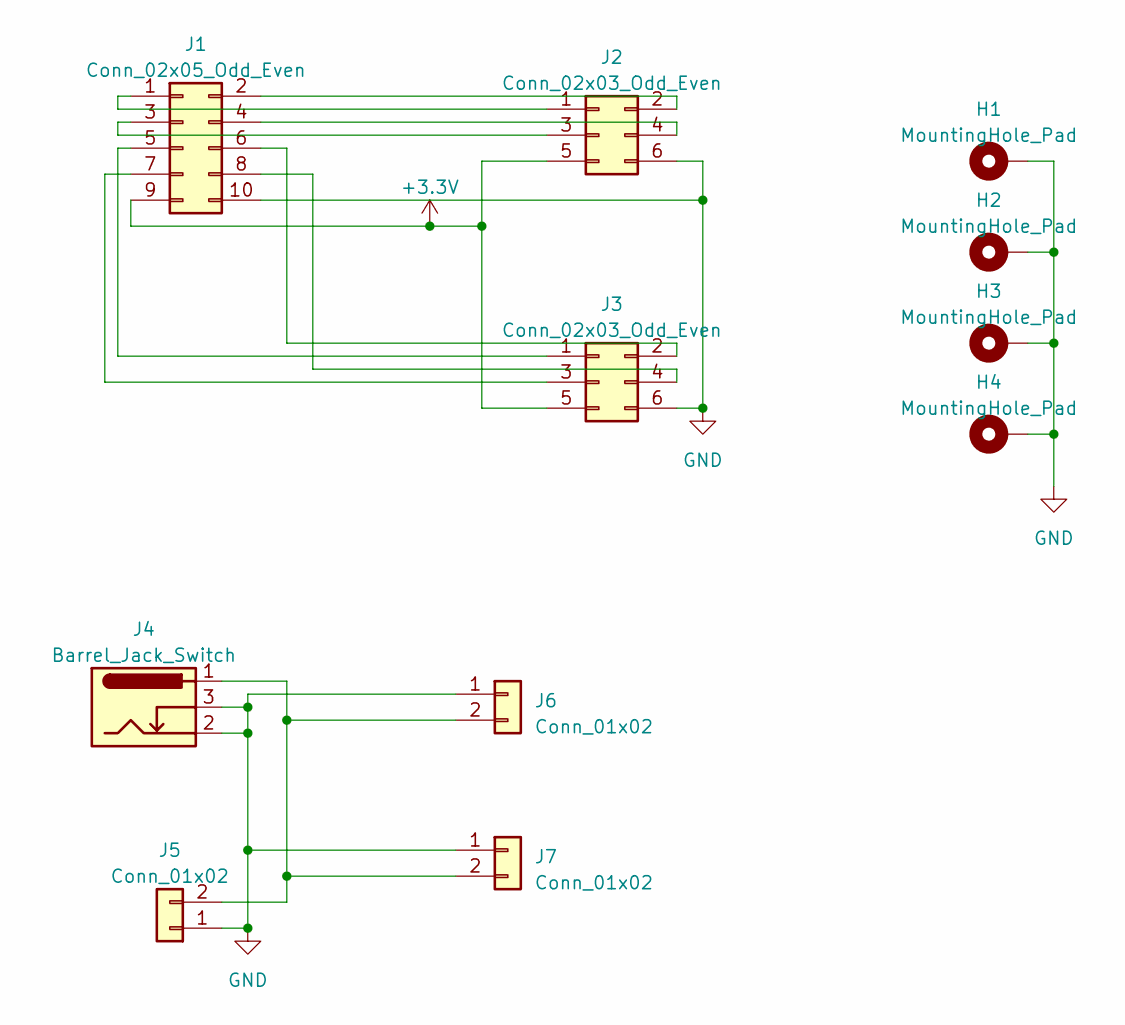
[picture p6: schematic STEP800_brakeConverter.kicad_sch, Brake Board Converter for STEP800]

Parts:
H1, H2, H3, H4: MountingHole_Pad; MountingHole_3.2mm_M3_Pad_TopBottom
J1: Conn_02x05_Odd_Even; IDC-Header_2x05_P2.54mm_Vertical
J2, J3: Conn_02x03_Odd_Even; IDC-Header_2x03_P2.54mm_Vertical
J4: Barrel_Jack_Switch; BarrelJack_GCT_DCJ200-10-A_Horizontal
J5, J6, J7: Conn_01x02; PhoenixContact_MCV_1,5_2-G-3.81_1x02_P3.81mm_Vertical

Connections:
+3.3V: J1.9, J2.5, J3.5
GND: H1.1, H2.1, H3.1, H4.1, J1.10, J2.6, J3.6, J4.2, J4.3, J5.1, J6.1, J7.1
unnamed: J1.1, J2.1
unnamed: J1.2, J2.2
unnamed: J1.3, J2.3
unnamed: J1.4, J2.4
unnamed: J1.5, J3.1
unnamed: J1.6, J3.2
unnamed: J1.7, J3.3
unnamed: J1.8, J3.4
unnamed: J4.1, J5.2, J6.2, J7.2

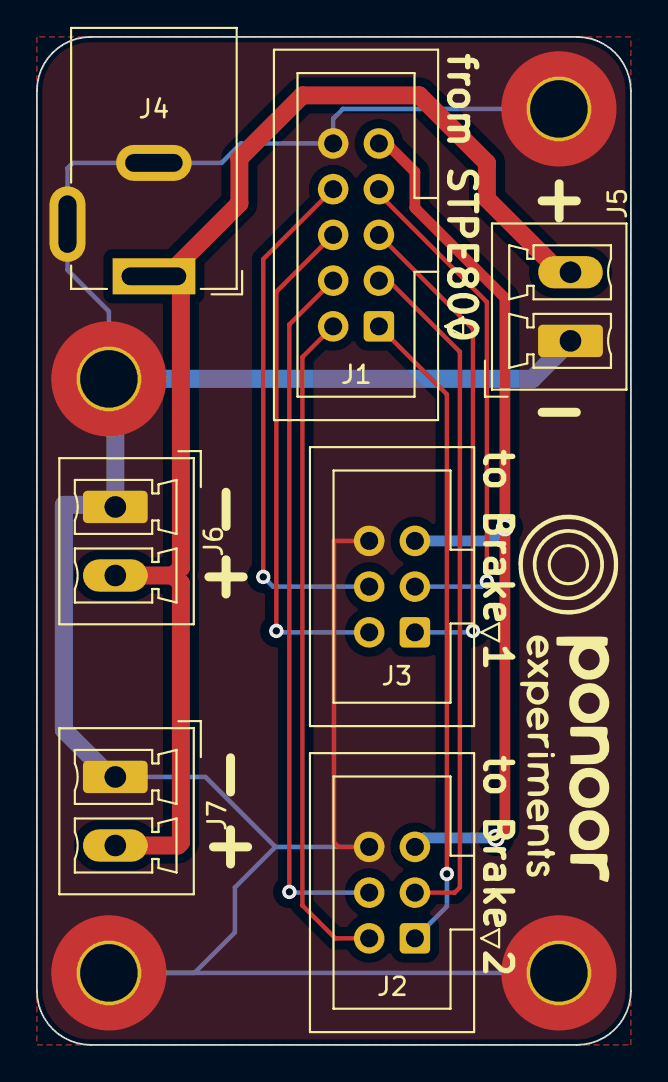
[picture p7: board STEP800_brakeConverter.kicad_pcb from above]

Board: 2 copper layers, 33.0 x 56.0 mm, 11 parts (0 on the bottom side), 11 nets.

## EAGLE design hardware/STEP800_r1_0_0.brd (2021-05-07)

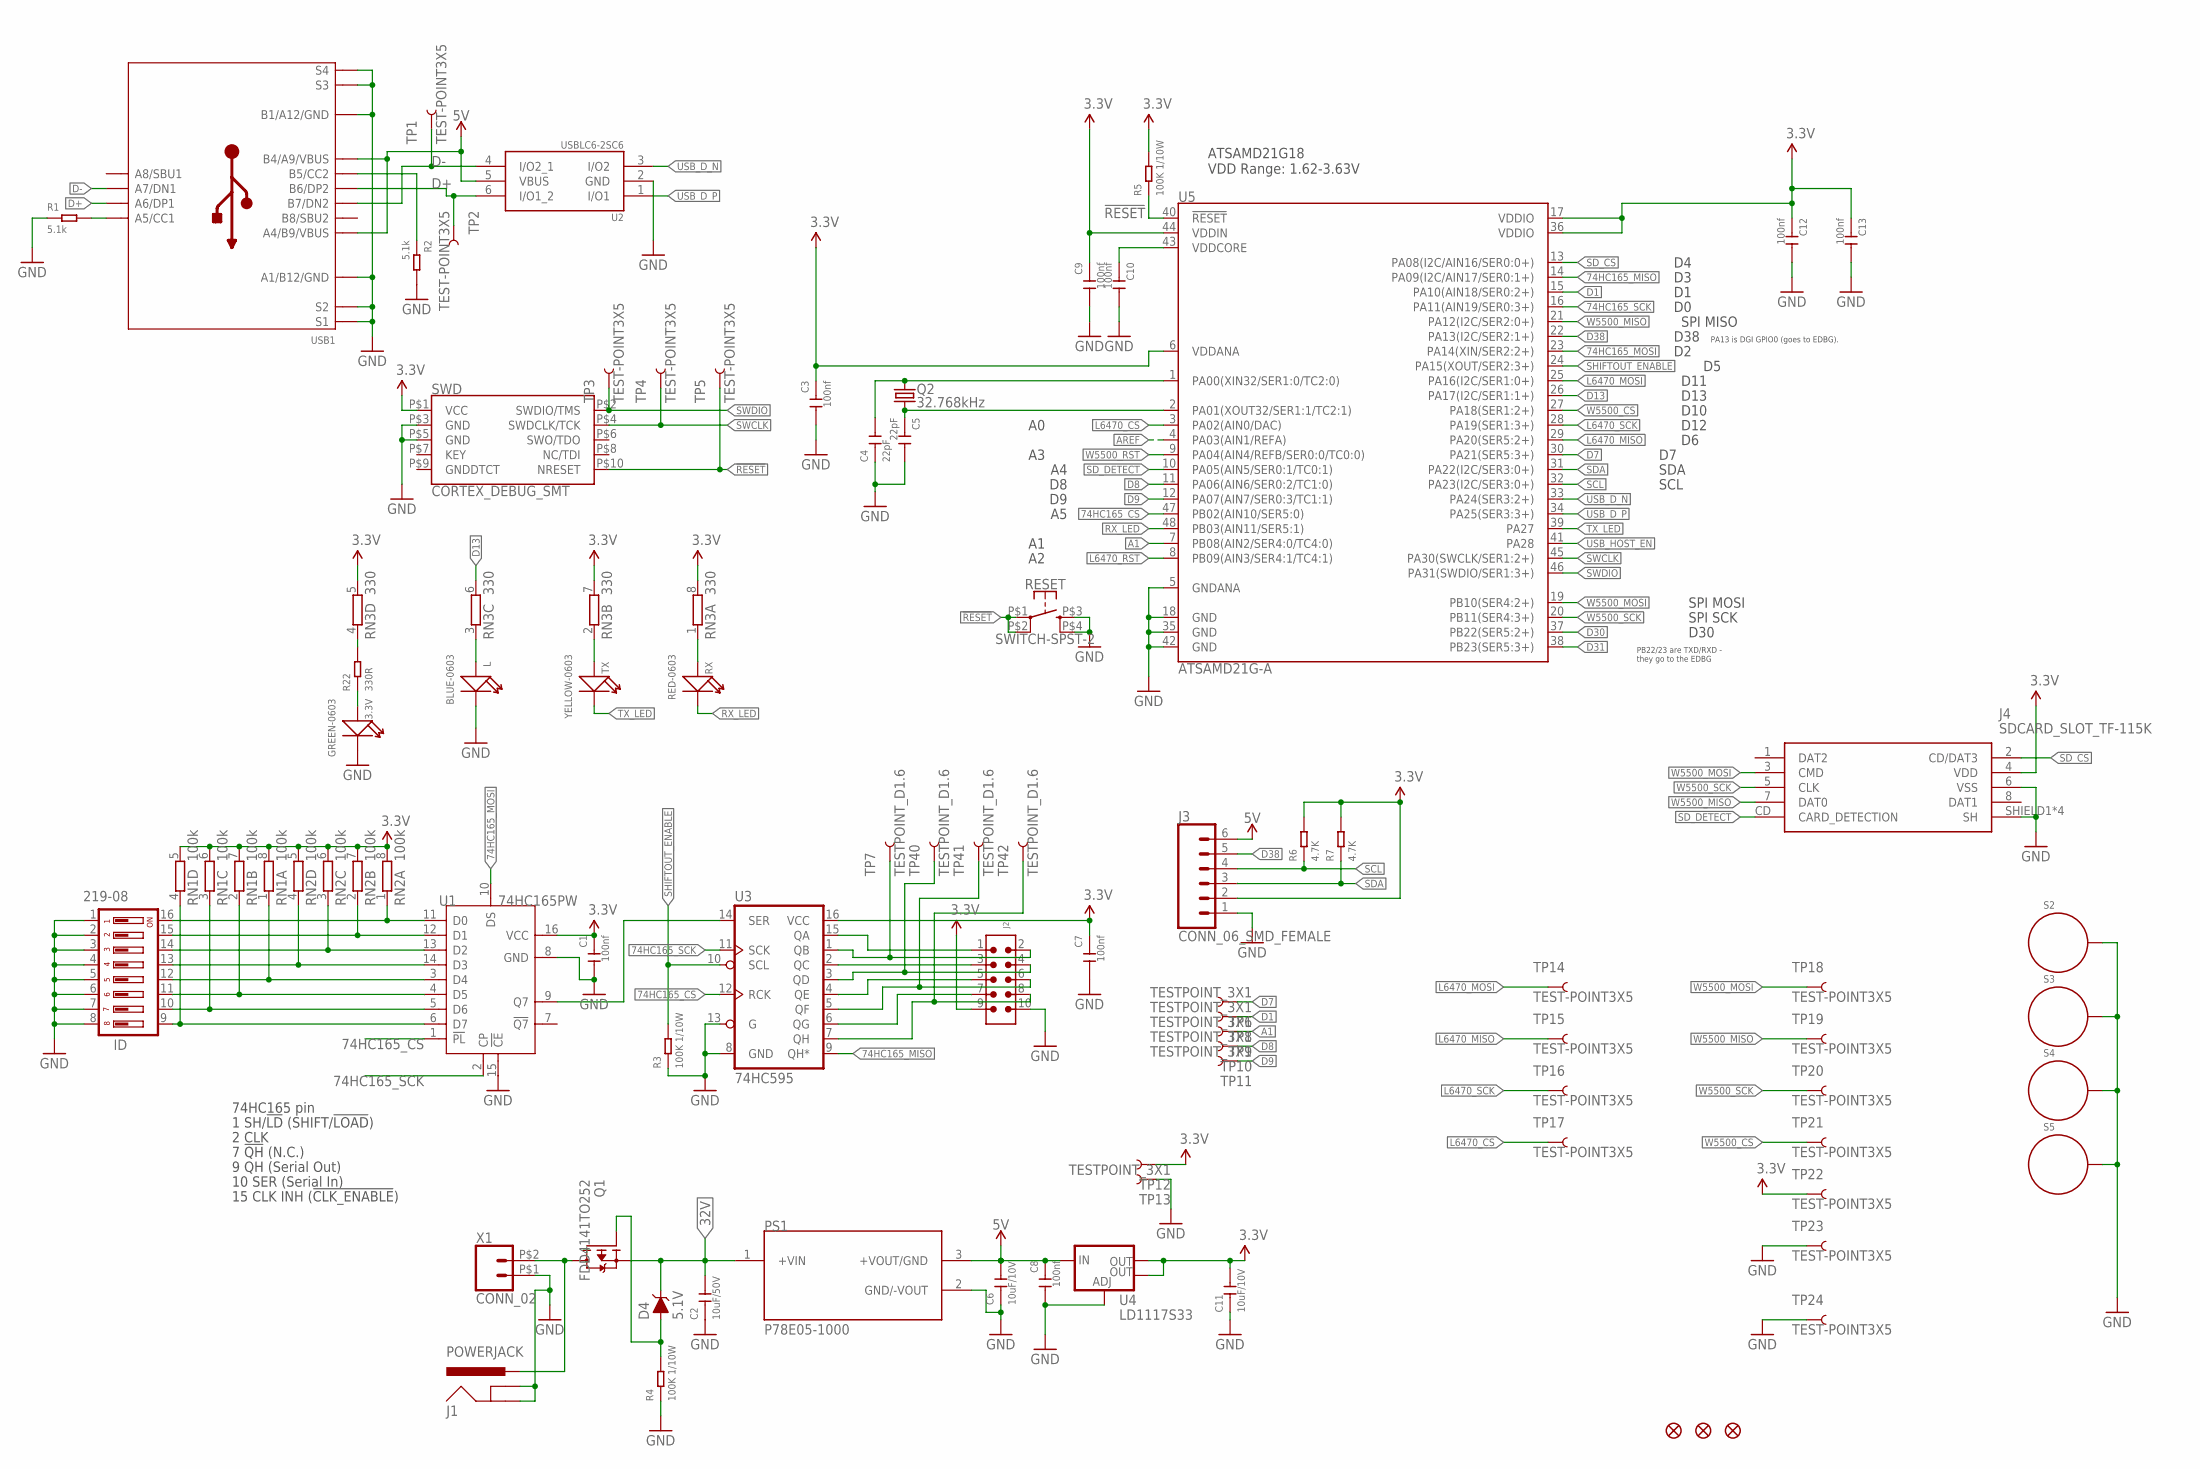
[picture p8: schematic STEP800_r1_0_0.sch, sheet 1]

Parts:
3.3V: GREEN-0603; LED-0603
C1, C3, C7, C8, C9, C10, C12, C13: 100nf; C0402
C2: 10uF/50V; C1206
C4, C5: 22pF; C0402
C6: 10uF/10V; C1206
C11: 10uF/10V; C0805
D4: 5.1V; SOD-323
FD1, FD2, FD3: FIDUCIAL1X2; FIDUCIAL-1X2
ID: 219-08; CTS-219-08
J1: POWERJACK; POWERJACK_SLOT
J2: 6120XX21621_61201021621; 61201021621
J3: CONN_06_SMD_FEMALE; 1X06-SMD-FEMALE
J4: SDCARD_SLOT_TF-115K; TF-115K
L: BLUE-0603; LED-0603
PS1: P78E05-1000; CONV_P78E05-1000
Q1: FDD4141TO252; TO252
Q2: 32.768kHz; FC-135
R1, R2: 5.1k; R0603
R3, R4, R5: 100K 1/10W; R0603
R6, R7: 4.7K; R0603
R22: 330R; R0603
RESET: SWITCH-SPST-2; SKRP
RN1, RN2: 100k; CAY16_LONG_W
RN3: 330; CAY16_LONG_W
RX: RED-0603; LED-0603
S2, S3, S4, S5: STANDOFF_ELECTRICAL; STANDOFF-ELECTRICAL
SWD: CORTEX_DEBUG_SMT; 20021121-00010C4LF
TP1, TP2, TP3, TP4, TP5, TP14, TP15, TP16, TP17, TP18, TP19, TP20, TP21, TP22, TP23, TP24: TEST-POINT3X5; PAD.03X.05
TP6, TP8, TP9, TP10, TP11, TP12, TP13: TESTPOINT_3X1
TP7, TP40, TP41, TP42: TESTPOINT_D1.6
TX: YELLOW-0603; LED-0603
U1: 74HC165PW; TSSOP16
U2: USBLC6-2SC6; SOT23-6L
U3: 74HC595; TSSOP16
U4: LD1117S33; SOT223
U5: ATSAMD21G-A; TQFP-48
USB1: USB-C_USB2.0-TYPE-C
X1: CONN_02; WJ25C-B-7.62-2P

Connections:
3.3V: C1.1, C3.1, C7.1, C9.1, C11.2, C12.1, C13.1, J2.9, J3.2, J4.4 (VDD), R5.2, R6.2, R7.2, RN1.5 (2), RN1.6 (2), RN1.7 (2), RN1.8 (2), RN2.5 (2), RN2.6 (2), RN2.7 (2), RN2.8 (2), RN3.5 (2), RN3.7 (2), RN3.8 (2), SWD.P$1 (VCC), TP12.P$1, TP22.P$1, U1.16 (VCC), U3.16 (VCC), U4.2 (OUT), U4.4 (OUT), U5.6 (VDDANA), U5.17 (VDDIO), U5.36 (VDDIO), U5.44 (VDDIN); also elsewhere on the board
5V: C6.2, C8.1, J3.6, PS1.3 (+VOUT/GND), U2.5 (VBUS), U4.3 (IN), USB1.A4_B9 (A4/B9/VBUS), USB1.B4_A9 (B4/A9/VBUS); also elsewhere on the board
32V: C2.2, D4.C, PS1.1 (+VIN), Q1.2 (S); also elsewhere on the board
74HC165_CS: U1.1 (!PL), U3.12 (RCK), U5.47 (PB02(AIN10/SER5:0))
74HC165_MISO: U3.9 (QH*), U5.14 (PA09(I2C/AIN17/SER0:1+))
74HC165_MOSI: U1.10 (DS), U5.23 (PA14(XIN/SER2:2+))
74HC165_SCK: U1.2 (CP), U3.11 (SCK), U5.16 (PA11(AIN19/SER0:3+))
!RESET: R5.1, RESET.P$1 (1), RESET.P$2 (2), SWD.P$10 (NRESET), TP5.P$1, U5.40 (!RESET!)
A1: TP9.P$1, U5.7 (PB08(AIN2/SER4:0/TC4:0))
AREF: U5.4 (PA03(AIN1/REFA))
D1: TP8.P$1, U5.15 (PA10(AIN18/SER0:2+))
D7: TP6.P$1, U5.30 (PA21(SER5:3+))
D8: TP10.P$1, U5.11 (PA06(AIN6/SER0:2/TC1:0))
D9: TP11.P$1, U5.12 (PA07(AIN7/SER0:3/TC1:1))
D13: RN3.6 (2), U5.26 (PA17(I2C/SER1:1+))
D30: U5.37 (PB22(SER5:2+))
D31: U5.38 (PB23(SER5:3+))
D38: J3.5, U5.22 (PA13(I2C/SER2:1+))
D+: TP2.P$1, U2.6 (I/O1_2), USB1.A6 (A6/DP1), USB1.B6 (B6/DP2)
D-: TP1.P$1, U2.4 (I/O2_1), USB1.A7 (A7/DN1), USB1.B7 (B7/DN2)
GND: 3.3V.-, C1.2, C2.1, C3.2, C4.1, C5.2, C6.1, C7.2, C8.2, C9.2, C10.2, C11.1, C12.2, C13.2, ID.1, ID.2, ID.3, ID.4, ID.5, ID.6, ID.7, ID.8, J1.P$33 (GNDBREAK), J1.P$34 (GNDBREAK), J1.P$35 (GNDBREAK), J1.P$36 (GNDBREAK), J1.P$37 (GNDBREAK), J1.P$38 (GNDBREAK), J1.P$39 (GNDBREAK), J1.P$40 (GNDBREAK), J1.P$41 (GNDBREAK), J1.P$42 (GNDBREAK), J1.P$43 (GNDBREAK), J1.P$44 (GNDBREAK), J1.P$45 (GNDBREAK), J1.P$46 (GNDBREAK), J1.P$47 (GNDBREAK), J1.P$48 (GNDBREAK), J1.P$49 (GNDBREAK), J1.P$50 (GNDBREAK), J1.P$51 (GNDBREAK), J1.P$52 (GNDBREAK), J1.P$53 (GNDBREAK), J1.P$54 (GNDBREAK), J1.P$55 (GNDBREAK), J1.P$56 (GNDBREAK), J1.P$63 (GND), J1.P$64 (GND), J1.P$65 (GND), J1.P$66 (GND), J1.P$67 (GND), J1.P$68 (GND), J1.P$69 (GND), J1.P$70 (GND), J1.P$71 (GND), J1.P$72 (GND), J1.P$73 (GND), J1.P$74 (GND), J1.P$75 (GND), J1.P$76 (GND), J1.P$77 (GND), J1.P$78 (GND), J1.P$79 (GND), J1.P$80 (GND), J1.P$81 (GND), J1.P$82 (GND), J1.P$83 (GND), J1.P$84 (GND), J1.P$85 (GND), J2.10, J3.1, J4.6 (VSS), J4.SHIELD1 (SH), J4.SHIELD2 (SH), J4.SHIELD3 (SH), J4.SHIELD4 (SH), L.-, PS1.2 (GND/-VOUT), R1.1, R2.2, R3.1, R4.1, RESET.P$3 (3), RESET.P$4 (4), S2.P1, S3.P1, S4.P1, S5.P1, SWD.P$3 (GND), SWD.P$5 (GND), TP13.P$1, TP23.P$1, TP24.P$1, U1.8 (GND), U1.15 (!CE), U2.2 (GND), U3.8 (GND), U3.13 (G), U4.1 (ADJ), U5.5 (GNDANA), U5.18 (GND), U5.35 (GND), U5.42 (GND), USB1.A1_B12 (A1/B12/GND), USB1.B1_A12 (B1/A12/GND), USB1.S7 (S1), USB1.S8 (S1), USB1.S9 (S1), USB1.S10 (S1), USB1.S11 (S1), USB1.S12 (S1), USB1.S13 (S1), USB1.S14 (S1), USB1.S15 (S1), USB1.S16 (S3), USB1.S17 (S3), USB1.S18 (S3), USB1.S19 (S3), USB1.S20 (S3), USB1.S21 (S3), USB1.S22 (S3), USB1.S23 (S3), USB1.S24 (S3), USB1.S25 (S3), USB1.S26 (S3), USB1.S27 (S3), USB1.S29 (S2), USB1.S30 (S2), USB1.S31 (S2), USB1.S32 (S2), USB1.S33 (S2), USB1.S34 (S2), USB1.S35 (S2), USB1.S36 (S2), USB1.S37 (S4), USB1.S38 (S4), USB1.S39 (S4), USB1.S40 (S4), USB1.S41 (S4), USB1.S42 (S4), USB1.S43 (S4), USB1.S44 (S4), USB1.S45 (S4), USB1.S46 (S4), USB1.S47 (S4), USB1.S48 (S4), X1.P$1 (1); also elsewhere on the board
L6470_CS: TP17.P$1, U5.3 (PA02(AIN0/DAC)); also elsewhere on the board
L6470_MISO: TP15.P$1, U5.29 (PA20(SER5:2+)); also elsewhere on the board
L6470_MOSI: TP14.P$1, U5.25 (PA16(I2C/SER1:0+)); also elsewhere on the board
L6470_RST: U5.8 (PB09(AIN3/SER4:1/TC4:1)); also elsewhere on the board
L6470_SCK: TP16.P$1, U5.28 (PA19(SER1:3+)); also elsewhere on the board
unnamed: C4.2, Q2.P$2 (2), U5.1 (PA00(XIN32/SER1:0/TC2:0))
unnamed: ID.16, RN2.1, U1.11 (D0)
unnamed: D4.A, Q1.1 (G), R4.2
unnamed: ID.15, RN2.2 (1), U1.12 (D1)
unnamed: ID.14, RN2.3 (1), U1.13 (D2)
unnamed: C5.1, Q2.P$1 (1), U5.2 (PA01(XOUT32/SER1:1/TC2:1))
unnamed: U1.9 (Q7), U3.14 (SER)
unnamed: RN3.1, RX.+
unnamed: ID.13, RN2.4 (1), U1.14 (D3)
unnamed: ID.12, RN1.1, U1.3 (D4)
unnamed: ID.11, RN1.2 (1), U1.4 (D5)
unnamed: RN3.2 (1), TX.+
unnamed: L.+, RN3.3 (1)
unnamed: R22.2, RN3.4 (1)
unnamed: J2.3, U3.2 (QC)
unnamed: ID.10, RN1.3 (1), U1.5 (D6)
unnamed: J2.2, TP7.1, U3.1 (QB)
unnamed: J2.1, U3.15 (QA)
unnamed: ID.9, RN1.4 (1), U1.6 (D7)
unnamed: J2.4, TP40.1, U3.3 (QD)
unnamed: J2.5, U3.4 (QE)
unnamed: J2.6, TP41.1, U3.5 (QF)
unnamed: J2.7, U3.6 (QG)
unnamed: J2.8, TP42.1, U3.7 (QH)
unnamed: R2.1, USB1.B5 (B5/CC2)
unnamed: 3.3V.+, R22.1
unnamed: R1.2, USB1.A5 (A5/CC1)
RX_LED: RX.-, U5.48 (PB03(AIN11/SER5:1))
SCL: J3.4, R6.1, U5.32 (PA23(I2C/SER3:0+))
SDA: J3.3, R7.1, U5.31 (PA22(I2C/SER3:0+))
SD_CS: J4.2 (CD/DAT3), U5.13 (PA08(I2C/AIN16/SER0:0+))
SD_DETECT: J4.CD (CARD_DETECTION), U5.10 (PA05(AIN5/SER0:1/TC0:1))
SHIFTOUT_ENABLE: R3.2, U3.10 (SCL), U5.24 (PA15(XOUT/SER2:3+))
SWCLK: SWD.P$4 (SWDCLK/TCK), TP4.P$1, U5.45 (PA30(SWCLK/SER1:2+))
SWDIO: SWD.P$2 (SWDIO/TMS), TP3.P$1, U5.46 (PA31(SWDIO/SER1:3+))
TX_LED: TX.-, U5.39 (PA27)
USB_D_N: U2.3 (I/O2), U5.33 (PA24(SER3:2+))
USB_D_P: U2.1 (I/O1), U5.34 (PA25(SER3:3+))
USB_HOST_EN: U5.41 (PA28)
VDDCORE1: C10.1, U5.43 (VDDCORE)
VRAW: J1.P$2 (PWR), J1.P$3 (PWR), J1.P$4 (PWR), J1.P$5 (PWR), J1.P$6 (PWR), J1.P$7 (PWR), J1.P$8 (PWR), J1.P$9 (PWR), J1.P$10 (PWR), J1.P$11 (PWR), J1.P$12 (PWR), J1.P$13 (PWR), J1.P$14 (PWR), J1.P$15 (PWR), J1.P$16 (PWR), J1.P$17 (PWR), J1.P$18 (PWR), J1.P$19 (PWR), J1.P$20 (PWR), J1.P$21 (PWR), J1.P$22 (PWR), J1.P$23 (PWR), J1.P$24 (PWR), J1.P$25 (PWR), J1.P$26 (PWR), J1.P$27 (PWR), J1.P$28 (PWR), Q1.3 (D), X1.P$2 (2)
W5500_CS: TP21.P$1, U5.27 (PA18(SER1:2+)); also elsewhere on the board
W5500_MISO: J4.7 (DAT0), TP19.P$1, U5.21 (PA12(I2C/SER2:0+)); also elsewhere on the board
W5500_MOSI: J4.3 (CMD), TP18.P$1, U5.19 (PB10(SER4:2+)); also elsewhere on the board
W5500_RST: U5.9 (PA04(AIN4/REFB/SER0:0/TC0:0)); also elsewhere on the board
W5500_SCK: J4.5 (CLK), TP20.P$1, U5.20 (PB11(SER4:3+)); also elsewhere on the board

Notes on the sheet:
PB22/23 are TXD/RXD - they go to the EDBG
PA13 is DGI GPIO0 (goes to EDBG).
ATSAMD21G18 VDD Range: 1.62-3.63V
D30
D12
D10
D11
D13
D38
SPI MISO
SPI MOSI
SPI SCK
SDA
SCL
1 SH/!LD! (SHIFT/!LOAD!)
2 CLK
7 !QH! (N.C.)
9 QH (Serial Out)
10 SER (Serial In)
15 CLK INH (!CLK_ENABLE!)
74HC165 pin

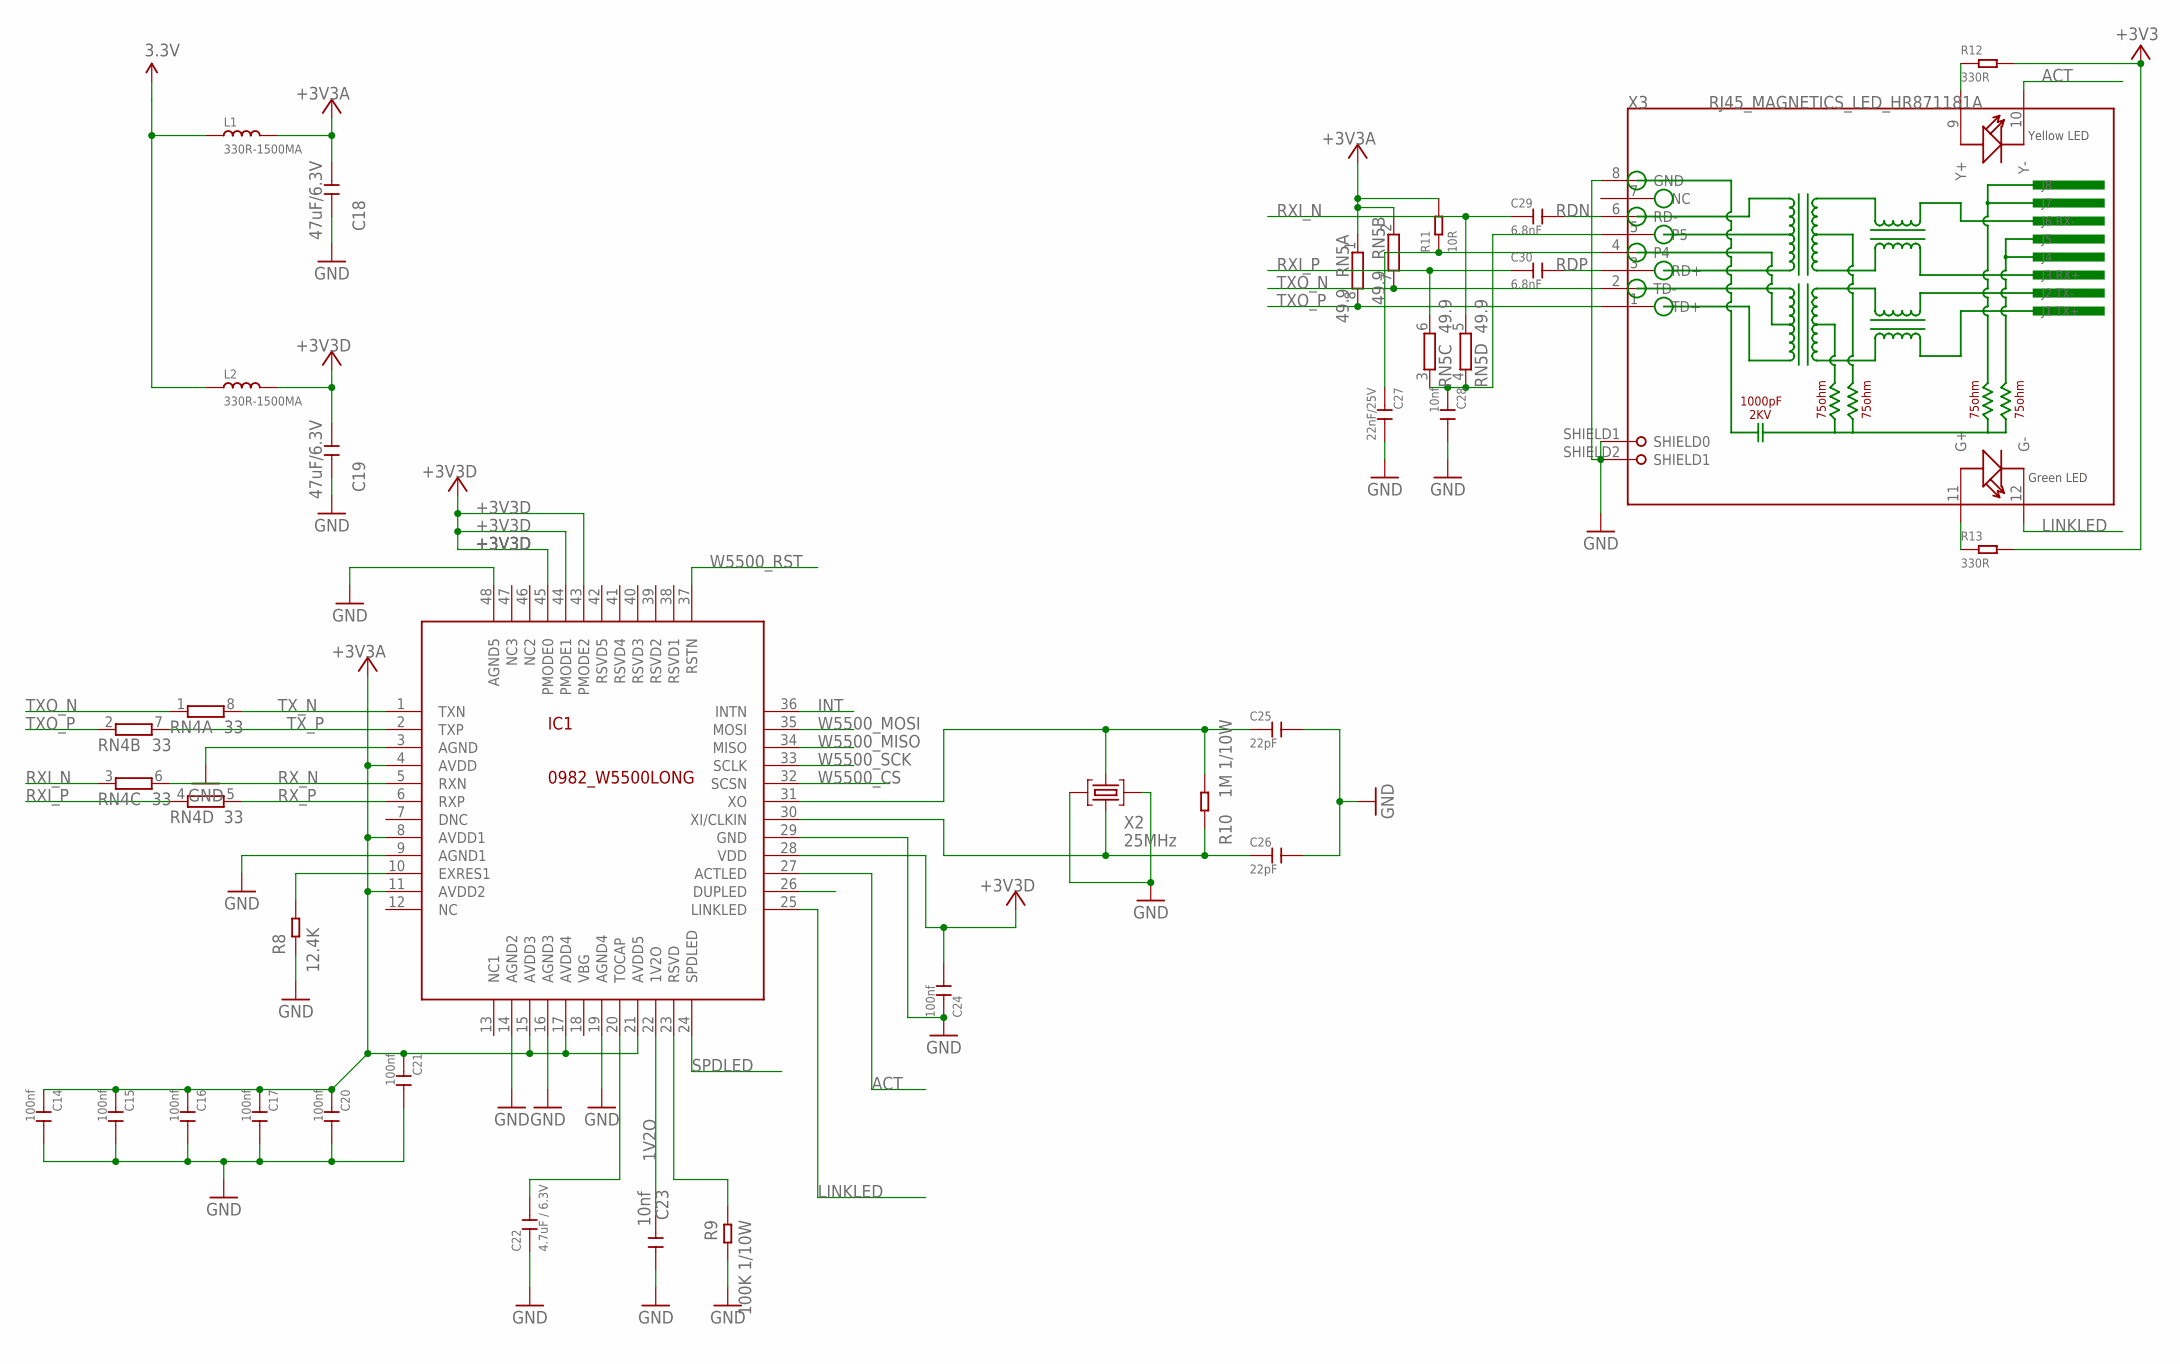
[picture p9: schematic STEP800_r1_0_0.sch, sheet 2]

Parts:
C14, C15, C16, C17, C20, C21, C24: 100nf; C0402
C18, C19: 47uF/6.3V; C1206
C22: 4.7uF / 6.3V; C0603
C23, C28: 10nf; C0603
C25, C26: 22pF; C0402
C27: 22nF/25V; C0402
C29, C30: 6.8nF; C0402
IC1: 0982_W5500LONG; TQFP48-LONG
L1, L2: 330R-1500MA; L0805
R8: 12.4K; R0603
R9: 100K 1/10W; R0603
R10: 1M 1/10W; R0603
R11: 10R; R0603
R12, R13: 330R; R0603
RN4: 33; CAY16_LONG_W
RN5: 49.9; CAY16_LONG_W
X2: 25MHz; CRYSTAL-3.2-2.5
X3: RJ45_MAGNETICS_LED_HR871181A; HR871181A

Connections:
1V2O: C23.2, IC1.22 (1V2O)
3.3V: L1.1, L2.1, R12.2, R13.2; also elsewhere on the board
+3V3A: C14.1, C15.1, C16.1, C17.1, C18.1, C20.1, C21.1, IC1.4 (AVDD), IC1.8 (AVDD1), IC1.11 (AVDD2), IC1.15 (AVDD3), IC1.17 (AVDD4), IC1.21 (AVDD5), L1.2, R11.2, RN5.1, RN5.2 (1)
+3V3D: C19.1, C24.2, IC1.28 (VDD), IC1.43 (PMODE2), IC1.44 (PMODE1), IC1.45 (PMODE0), L2.2
ACT: IC1.27 (ACTLED), X3.10 (Y-)
FDXLED1: IC1.26 (DUPLED)
GND: C14.2, C15.2, C16.2, C17.2, C18.2, C19.2, C20.2, C21.2, C22.1, C23.1, C24.1, C25.2, C26.2, C27.2, C28.2, IC1.3 (AGND), IC1.9 (AGND1), IC1.14 (AGND2), IC1.16 (AGND3), IC1.19 (AGND4), IC1.29 (GND), IC1.48 (AGND5), R8.1, R9.1, X2.2 (GND), X2.4 (GND), X3.8 (GND), X3.SHIELD1 (SHIELD0), X3.SHIELD2 (SHIELD1); also elsewhere on the board
INT: IC1.36 (INTN)
LINKLED: IC1.25 (LINKLED), X3.12 (G-)
unnamed: C25.1, IC1.31 (XO), R10.1, X2.3 (C2)
unnamed: IC1.23 (RSVD), R9.2
unnamed: IC1.10 (EXRES1), R8.2
unnamed: C22.2, IC1.20 (TOCAP)
unnamed: C27.1, R11.1, X3.4
unnamed: C28.1, RN5.3 (1), RN5.4 (1), X3.5
unnamed: R12.1, X3.9 (Y+)
unnamed: R13.1, X3.11 (G+)
NC: IC1.12 (NC)
OSC2E1: C26.1, IC1.30 (XI/CLKIN), R10.2, X2.1 (C1)
RDN: C29.2, X3.6 (RD-)
RDP: C30.2, X3.3 (RD+)
RSVD1: IC1.38 (RSVD1)
RSVD2: IC1.39 (RSVD2)
RSVD3: IC1.40 (RSVD3)
RXI_N: C29.1, RN4.3 (1), RN5.5 (2)
RXI_P: C30.1, RN4.4 (1), RN5.6 (2)
RX_N: IC1.5 (RXN), RN4.6 (2)
RX_P: IC1.6 (RXP), RN4.5 (2)
SPDLED: IC1.24 (SPDLED)
TXO_N: RN4.1, RN5.7 (2), X3.2 (TD-)
TXO_P: RN4.2 (1), RN5.8 (2), X3.1 (TD+)
TX_N: IC1.1 (TXN), RN4.8 (2)
TX_P: IC1.2 (TXP), RN4.7 (2)
W5500_CS: IC1.32 (SCSN); also elsewhere on the board
W5500_MISO: IC1.34 (MISO); also elsewhere on the board
W5500_MOSI: IC1.35 (MOSI); also elsewhere on the board
W5500_RST: IC1.37 (RSTN); also elsewhere on the board
W5500_SCK: IC1.33 (SCLK); also elsewhere on the board

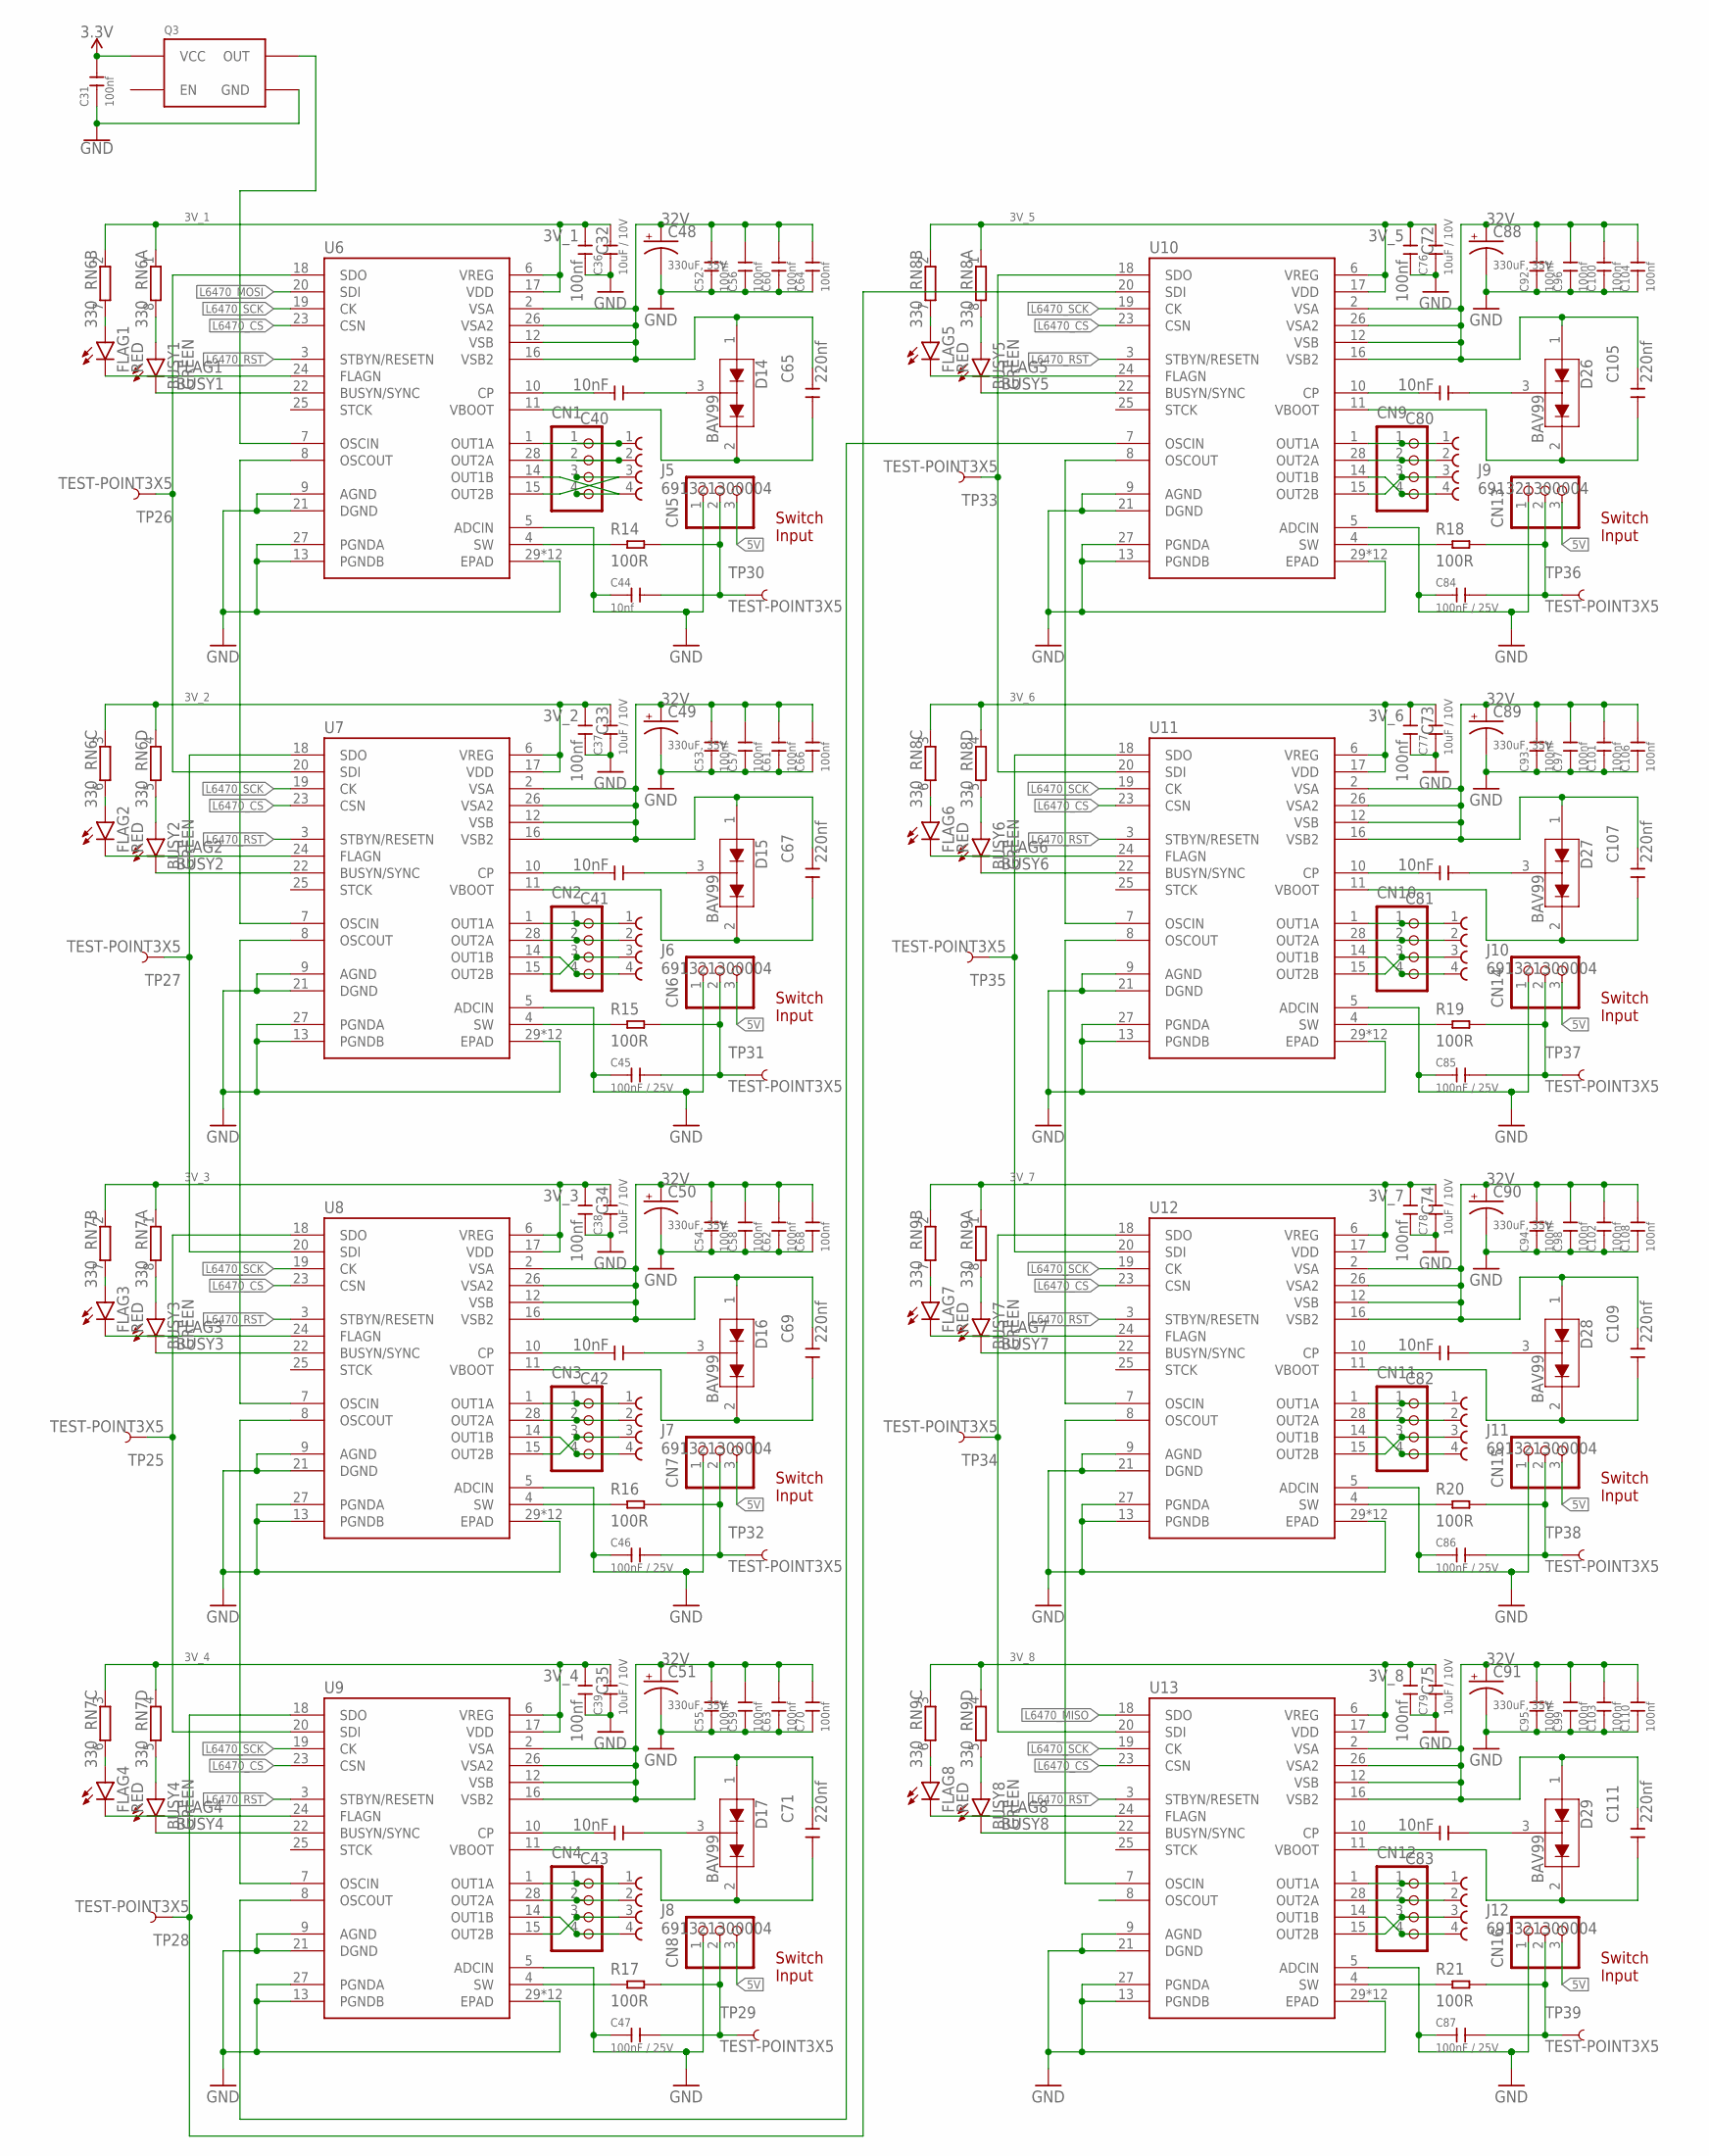
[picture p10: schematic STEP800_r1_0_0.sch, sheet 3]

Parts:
BUSY1, BUSY2, BUSY3, BUSY4, BUSY5, BUSY6, BUSY7, BUSY8: GREEN; LED-0603
C31, C32, C33, C34, C35, C72, C73, C74, C75: 100nf; C0402
C36, C37, C38, C39, C76, C77, C78, C79: 10uF / 10V; C0805
C40, C41, C42, C43, C80, C81, C82, C83: 10nF; C0603
C44: 10nf; C0402
C45, C46, C47, C84, C85, C86, C87: 100nF / 25V; C0402
C48, C49, C50, C51, C88, C89, C90, C91: 330uF, 35V; NICHICON_D10
C52, C53, C54, C55, C56, C57, C58, C59, C60, C61, C62, C63, C64, C66, C68, C70, C92, C93, C94, C95, C96, C97, C98, C99, C100, C101, C102, C103, C104, C106, C108, C110: 100nf; C0603
C65, C67, C69, C71, C105, C107, C109, C111: 220nf; C0603
CN1, CN2, CN3, CN4, CN9, CN10, CN11, CN12: B4B-XASK-1
CN5, CN6, CN7, CN8, CN13, CN14, CN15, CN16: B3B-XASK-1
D14, D15, D16, D17, D26, D27, D28, D29: BAV99; SOT23-3
FLAG1, FLAG2, FLAG3, FLAG4, FLAG5, FLAG6, FLAG7, FLAG8: RED; LED-0603
J5, J6, J7, J8, J9, J10, J11, J12: 691321300004
Q3: CRYSTAL_OSC_SG5032; SG5032
R14, R15, R16, R17, R18, R19, R20, R21: 100R; R0603
RN6, RN7, RN8, RN9: 330; CAY16_LONG_W
TP25, TP26, TP27, TP28, TP29, TP30, TP31, TP32, TP33, TP34, TP35, TP36, TP37, TP38, TP39: TEST-POINT3X5; PAD.03X.05
U6, U7, U8, U9, U10, U11, U12, U13: L6470_THERMALVIA; HTSSOP28_VIA

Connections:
3.3V: C31.2, Q3.4 (VCC); also elsewhere on the board
3V_1: C32.1, C36.2, RN6.1, RN6.2 (1), U6.6 (VREG), U6.17 (VDD)
3V_2: C33.1, C37.2, RN6.3 (1), RN6.4 (1), U7.6 (VREG), U7.17 (VDD)
3V_3: C34.1, C38.2, RN7.1, RN7.2 (1), U8.6 (VREG), U8.17 (VDD)
3V_4: C35.1, C39.2, RN7.3 (1), RN7.4 (1), U9.6 (VREG), U9.17 (VDD)
3V_5: C72.1, C76.2, RN8.1, RN8.2 (1), U10.6 (VREG), U10.17 (VDD)
3V_6: C73.1, C77.2, RN8.3 (1), RN8.4 (1), U11.6 (VREG), U11.17 (VDD)
3V_7: C74.1, C78.2, RN9.1, RN9.2 (1), U12.6 (VREG), U12.17 (VDD)
3V_8: C75.1, C79.2, RN9.3 (1), RN9.4 (1), U13.6 (VREG), U13.17 (VDD)
5V: CN5.3, CN6.3, CN7.3, CN8.3, CN13.3, CN14.3, CN15.3, CN16.3; also elsewhere on the board
32V: C48.+, C49.+, C50.+, C51.+, C52.2, C53.2, C54.2, C55.2, C56.2, C57.2, C58.2, C59.2, C60.2, C61.2, C62.2, C63.2, C64.2, C65.2, C66.2, C67.2, C68.2, C69.2, C70.2, C71.2, C88.+, C89.+, C90.+, C91.+, C92.2, C93.2, C94.2, C95.2, C96.2, C97.2, C98.2, C99.2, C100.2, C101.2, C102.2, C103.2, C104.2, C105.2, C106.2, C107.2, C108.2, C109.2, C110.2, C111.2, D14.1 (A1), D15.1 (A1), D16.1 (A1), D17.1 (A1), D26.1 (A1), D27.1 (A1), D28.1 (A1), D29.1 (A1), U6.2 (VSA), U6.12 (VSB), U6.16 (VSB2), U6.26 (VSA2), U7.2 (VSA), U7.12 (VSB), U7.16 (VSB2), U7.26 (VSA2), U8.2 (VSA), U8.12 (VSB), U8.16 (VSB2), U8.26 (VSA2), U9.2 (VSA), U9.12 (VSB), U9.16 (VSB2), U9.26 (VSA2), U10.2 (VSA), U10.12 (VSB), U10.16 (VSB2), U10.26 (VSA2), U11.2 (VSA), U11.12 (VSB), U11.16 (VSB2), U11.26 (VSA2), U12.2 (VSA), U12.12 (VSB), U12.16 (VSB2), U12.26 (VSA2), U13.2 (VSA), U13.12 (VSB), U13.16 (VSB2), U13.26 (VSA2); also elsewhere on the board
BUSY1: BUSY1.C, U6.22 (BUSYN/SYNC)
BUSY2: BUSY2.C, U7.22 (BUSYN/SYNC)
BUSY3: BUSY3.C, U8.22 (BUSYN/SYNC)
BUSY4: BUSY4.C, U9.22 (BUSYN/SYNC)
BUSY5: BUSY5.C, U10.22 (BUSYN/SYNC)
BUSY6: BUSY6.C, U11.22 (BUSYN/SYNC)
BUSY7: BUSY7.C, U12.22 (BUSYN/SYNC)
BUSY8: BUSY8.C, U13.22 (BUSYN/SYNC)
FLAG1: FLAG1.C, U6.24 (FLAGN)
FLAG2: FLAG2.C, U7.24 (FLAGN)
FLAG3: FLAG3.C, U8.24 (FLAGN)
FLAG4: FLAG4.C, U9.24 (FLAGN)
FLAG5: FLAG5.C, U10.24 (FLAGN)
FLAG6: FLAG6.C, U11.24 (FLAGN)
FLAG7: FLAG7.C, U12.24 (FLAGN)
FLAG8: FLAG8.C, U13.24 (FLAGN)
GND: C31.1, C32.2, C33.2, C34.2, C35.2, C36.1, C37.1, C38.1, C39.1, C44.1, C45.1, C46.1, C47.1, C48.-, C49.-, C50.-, C51.-, C52.1, C53.1, C54.1, C55.1, C56.1, C57.1, C58.1, C59.1, C60.1, C61.1, C62.1, C63.1, C64.1, C66.1, C68.1, C70.1, C72.2, C73.2, C74.2, C75.2, C76.1, C77.1, C78.1, C79.1, C84.1, C85.1, C86.1, C87.1, C88.-, C89.-, C90.-, C91.-, C92.1, C93.1, C94.1, C95.1, C96.1, C97.1, C98.1, C99.1, C100.1, C101.1, C102.1, C103.1, C104.1, C106.1, C108.1, C110.1, CN5.1, CN6.1, CN7.1, CN8.1, CN13.1, CN14.1, CN15.1, CN16.1, Q3.2 (GND), U6.5 (ADCIN), U6.9 (AGND), U6.13 (PGNDB), U6.21 (DGND), U6.27 (PGNDA), U6.29 (EPAD), U6.VIA1 (EPAD), U6.VIA2 (EPAD), U6.VIA3 (EPAD), U6.VIA4 (EPAD), U6.VIA5 (EPAD), U6.VIA6 (EPAD), U6.VIA7 (EPAD), U6.VIA8 (EPAD), U6.VIA9 (EPAD), U6.VIA10 (EPAD), U6.VIA11 (EPAD), U7.5 (ADCIN), U7.9 (AGND), U7.13 (PGNDB), U7.21 (DGND), U7.27 (PGNDA), U7.29 (EPAD), U7.VIA1 (EPAD), U7.VIA2 (EPAD), U7.VIA3 (EPAD), U7.VIA4 (EPAD), U7.VIA5 (EPAD), U7.VIA6 (EPAD), U7.VIA7 (EPAD), U7.VIA8 (EPAD), U7.VIA9 (EPAD), U7.VIA10 (EPAD), U7.VIA11 (EPAD), U8.5 (ADCIN), U8.9 (AGND), U8.13 (PGNDB), U8.21 (DGND), U8.27 (PGNDA), U8.29 (EPAD), U8.VIA1 (EPAD), U8.VIA2 (EPAD), U8.VIA3 (EPAD), U8.VIA4 (EPAD), U8.VIA5 (EPAD), U8.VIA6 (EPAD), U8.VIA7 (EPAD), U8.VIA8 (EPAD), U8.VIA9 (EPAD), U8.VIA10 (EPAD), U8.VIA11 (EPAD), U9.5 (ADCIN), U9.9 (AGND), U9.13 (PGNDB), U9.21 (DGND), U9.27 (PGNDA), U9.29 (EPAD), U9.VIA1 (EPAD), U9.VIA2 (EPAD), U9.VIA3 (EPAD), U9.VIA4 (EPAD), U9.VIA5 (EPAD), U9.VIA6 (EPAD), U9.VIA7 (EPAD), U9.VIA8 (EPAD), U9.VIA9 (EPAD), U9.VIA10 (EPAD), U9.VIA11 (EPAD), U10.5 (ADCIN), U10.9 (AGND), U10.13 (PGNDB), U10.21 (DGND), U10.27 (PGNDA), U10.29 (EPAD), U10.VIA1 (EPAD), U10.VIA2 (EPAD), U10.VIA3 (EPAD), U10.VIA4 (EPAD), U10.VIA5 (EPAD), U10.VIA6 (EPAD), U10.VIA7 (EPAD), U10.VIA8 (EPAD), U10.VIA9 (EPAD), U10.VIA10 (EPAD), U10.VIA11 (EPAD), U11.5 (ADCIN), U11.9 (AGND), U11.13 (PGNDB), U11.21 (DGND), U11.27 (PGNDA), U11.29 (EPAD), U11.VIA1 (EPAD), U11.VIA2 (EPAD), U11.VIA3 (EPAD), U11.VIA4 (EPAD), U11.VIA5 (EPAD), U11.VIA6 (EPAD), U11.VIA7 (EPAD), U11.VIA8 (EPAD), U11.VIA9 (EPAD), U11.VIA10 (EPAD), U11.VIA11 (EPAD), U12.5 (ADCIN), U12.9 (AGND), U12.13 (PGNDB), U12.21 (DGND), U12.27 (PGNDA), U12.29 (EPAD), U12.VIA1 (EPAD), U12.VIA2 (EPAD), U12.VIA3 (EPAD), U12.VIA4 (EPAD), U12.VIA5 (EPAD), U12.VIA6 (EPAD), U12.VIA7 (EPAD), U12.VIA8 (EPAD), U12.VIA9 (EPAD), U12.VIA10 (EPAD), U12.VIA11 (EPAD), U13.5 (ADCIN), U13.9 (AGND), U13.13 (PGNDB), U13.21 (DGND), U13.27 (PGNDA), U13.29 (EPAD), U13.VIA1 (EPAD), U13.VIA2 (EPAD), U13.VIA3 (EPAD), U13.VIA4 (EPAD), U13.VIA5 (EPAD), U13.VIA6 (EPAD), U13.VIA7 (EPAD), U13.VIA8 (EPAD), U13.VIA9 (EPAD), U13.VIA10 (EPAD), U13.VIA11 (EPAD); also elsewhere on the board
L6470_CS: U6.23 (CSN), U7.23 (CSN), U8.23 (CSN), U9.23 (CSN), U10.23 (CSN), U11.23 (CSN), U12.23 (CSN), U13.23 (CSN); also elsewhere on the board
L6470_MISO: U13.18 (SDO); also elsewhere on the board
L6470_MOSI: U6.20 (SDI); also elsewhere on the board
L6470_RST: U6.3 (STBYN/RESETN), U7.3 (STBYN/RESETN), U8.3 (STBYN/RESETN), U9.3 (STBYN/RESETN), U10.3 (STBYN/RESETN), U11.3 (STBYN/RESETN), U12.3 (STBYN/RESETN), U13.3 (STBYN/RESETN); also elsewhere on the board
L6470_SCK: U6.19 (CK), U7.19 (CK), U8.19 (CK), U9.19 (CK), U10.19 (CK), U11.19 (CK), U12.19 (CK), U13.19 (CK); also elsewhere on the board
unnamed: C40.2, U6.10 (CP)
unnamed: C40.1, D14.3 (COM)
unnamed: C65.1, D14.2 (C2), U6.11 (VBOOT)
unnamed: R14.1, U6.4 (SW)
unnamed: BUSY1.A, RN6.8 (2)
unnamed: FLAG1.A, RN6.7 (2)
unnamed: C44.2, CN5.2, R14.2, TP30.P$1
unnamed: CN1.1, J5.1, U6.1 (OUT1A)
unnamed: CN1.2, J5.2, U6.28 (OUT2A)
unnamed: CN1.4, J5.4, U6.14 (OUT1B)
unnamed: CN1.3, J5.3, U6.15 (OUT2B)
unnamed: TP26.P$1, U6.18 (SDO), U7.20 (SDI)
unnamed: C41.2, U7.10 (CP)
unnamed: C41.1, D15.3 (COM)
unnamed: C67.1, D15.2 (C2), U7.11 (VBOOT)
unnamed: R15.1, U7.4 (SW)
unnamed: BUSY2.A, RN6.5 (2)
unnamed: FLAG2.A, RN6.6 (2)
unnamed: C45.2, CN6.2, R15.2, TP31.P$1
unnamed: CN2.1, J6.1, U7.1 (OUT1A)
unnamed: CN2.2, J6.2, U7.28 (OUT2A)
unnamed: CN2.4, J6.4, U7.14 (OUT1B)
unnamed: CN2.3, J6.3, U7.15 (OUT2B)
unnamed: TP27.P$1, U7.18 (SDO), U8.20 (SDI)
unnamed: C42.2, U8.10 (CP)
unnamed: C42.1, D16.3 (COM)
unnamed: C69.1, D16.2 (C2), U8.11 (VBOOT)
unnamed: R16.1, U8.4 (SW)
unnamed: BUSY3.A, RN7.8 (2)
unnamed: FLAG3.A, RN7.7 (2)
unnamed: C46.2, CN7.2, R16.2, TP32.P$1
unnamed: CN3.1, J7.1, U8.1 (OUT1A)
unnamed: CN3.2, J7.2, U8.28 (OUT2A)
unnamed: CN3.4, J7.4, U8.14 (OUT1B)
unnamed: CN3.3, J7.3, U8.15 (OUT2B)
unnamed: TP25.P$1, U8.18 (SDO), U9.20 (SDI)
unnamed: C43.2, U9.10 (CP)
unnamed: C43.1, D17.3 (COM)
unnamed: C71.1, D17.2 (C2), U9.11 (VBOOT)
unnamed: R17.1, U9.4 (SW)
unnamed: BUSY4.A, RN7.5 (2)
unnamed: FLAG4.A, RN7.6 (2)
unnamed: C47.2, CN8.2, R17.2, TP29.P$1
unnamed: CN4.1, J8.1, U9.1 (OUT1A)
unnamed: CN4.2, J8.2, U9.28 (OUT2A)
unnamed: CN4.4, J8.4, U9.14 (OUT1B)
unnamed: CN4.3, J8.3, U9.15 (OUT2B)
unnamed: TP28.P$1, U9.18 (SDO), U10.20 (SDI)
unnamed: C80.2, U10.10 (CP)
unnamed: C80.1, D26.3 (COM)
unnamed: C105.1, D26.2 (C2), U10.11 (VBOOT)
unnamed: R18.1, U10.4 (SW)
unnamed: BUSY5.A, RN8.8 (2)
unnamed: FLAG5.A, RN8.7 (2)
unnamed: C84.2, CN13.2, R18.2, TP36.P$1
unnamed: CN9.1, J9.1, U10.1 (OUT1A)
unnamed: CN9.2, J9.2, U10.28 (OUT2A)
unnamed: CN9.4, J9.4, U10.14 (OUT1B)
unnamed: CN9.3, J9.3, U10.15 (OUT2B)
unnamed: TP33.P$1, U10.18 (SDO), U11.20 (SDI)
unnamed: C81.2, U11.10 (CP)
unnamed: C81.1, D27.3 (COM)
unnamed: C107.1, D27.2 (C2), U11.11 (VBOOT)
unnamed: R19.1, U11.4 (SW)
unnamed: BUSY6.A, RN8.5 (2)
unnamed: FLAG6.A, RN8.6 (2)
unnamed: C85.2, CN14.2, R19.2, TP37.P$1
unnamed: CN10.1, J10.1, U11.1 (OUT1A)
unnamed: CN10.2, J10.2, U11.28 (OUT2A)
unnamed: CN10.4, J10.4, U11.14 (OUT1B)
unnamed: CN10.3, J10.3, U11.15 (OUT2B)
unnamed: TP35.P$1, U11.18 (SDO), U12.20 (SDI)
unnamed: C82.2, U12.10 (CP)
unnamed: C82.1, D28.3 (COM)
unnamed: C109.1, D28.2 (C2), U12.11 (VBOOT)
unnamed: R20.1, U12.4 (SW)
unnamed: BUSY7.A, RN9.8 (2)
unnamed: FLAG7.A, RN9.7 (2)
unnamed: C86.2, CN15.2, R20.2, TP38.P$1
unnamed: CN11.1, J11.1, U12.1 (OUT1A)
unnamed: CN11.2, J11.2, U12.28 (OUT2A)
unnamed: CN11.4, J11.4, U12.14 (OUT1B)
unnamed: CN11.3, J11.3, U12.15 (OUT2B)
unnamed: TP34.P$1, U12.18 (SDO), U13.20 (SDI)
unnamed: C83.2, U13.10 (CP)
unnamed: C83.1, D29.3 (COM)
unnamed: C111.1, D29.2 (C2), U13.11 (VBOOT)
unnamed: R21.1, U13.4 (SW)
unnamed: BUSY8.A, RN9.5 (2)
unnamed: FLAG8.A, RN9.6 (2)
unnamed: C87.2, CN16.2, R21.2, TP39.P$1
unnamed: CN12.1, J12.1, U13.1 (OUT1A)
unnamed: CN12.2, J12.2, U13.28 (OUT2A)
unnamed: CN12.4, J12.4, U13.14 (OUT1B)
unnamed: CN12.3, J12.3, U13.15 (OUT2B)
OSCOUT2: U6.8 (OSCOUT), U7.7 (OSCIN)
OSCOUT4: U7.8 (OSCOUT), U8.7 (OSCIN)
OSCOUT6: U8.8 (OSCOUT), U9.7 (OSCIN)
OSCOUT8: U9.8 (OSCOUT), U10.7 (OSCIN)
OSCOUT10: U10.8 (OSCOUT), U11.7 (OSCIN)
OSCOUT12: U11.8 (OSCOUT), U12.7 (OSCIN)
OSCOUT14: U12.8 (OSCOUT), U13.7 (OSCIN)
OSCOUT16: U13.8 (OSCOUT)
QGOUT1: Q3.3 (OUT), U6.7 (OSCIN)

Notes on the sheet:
Switch Input

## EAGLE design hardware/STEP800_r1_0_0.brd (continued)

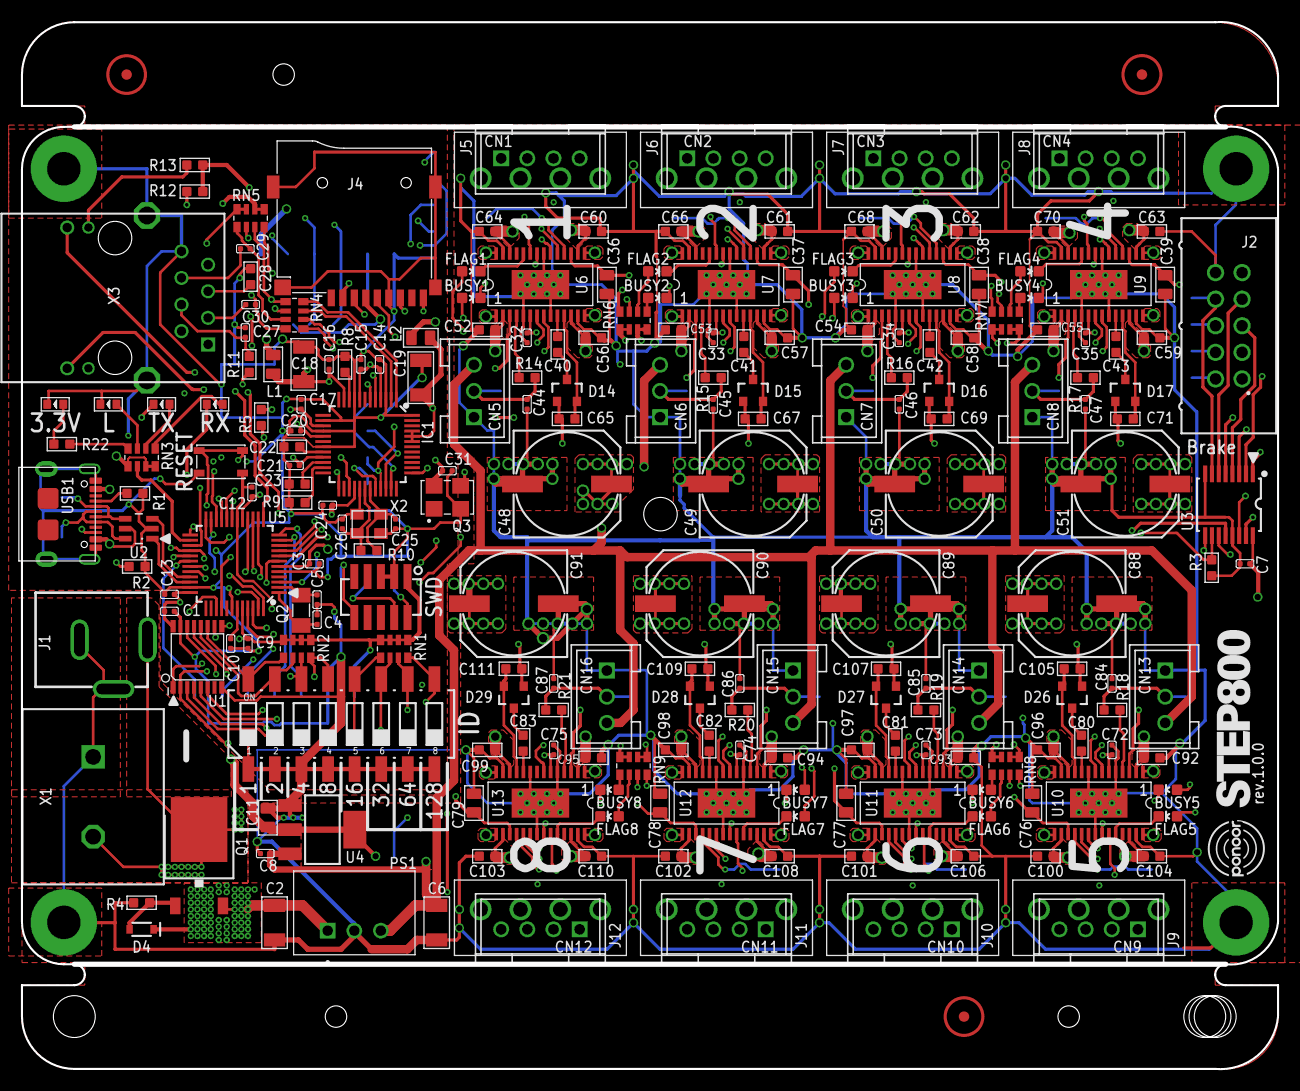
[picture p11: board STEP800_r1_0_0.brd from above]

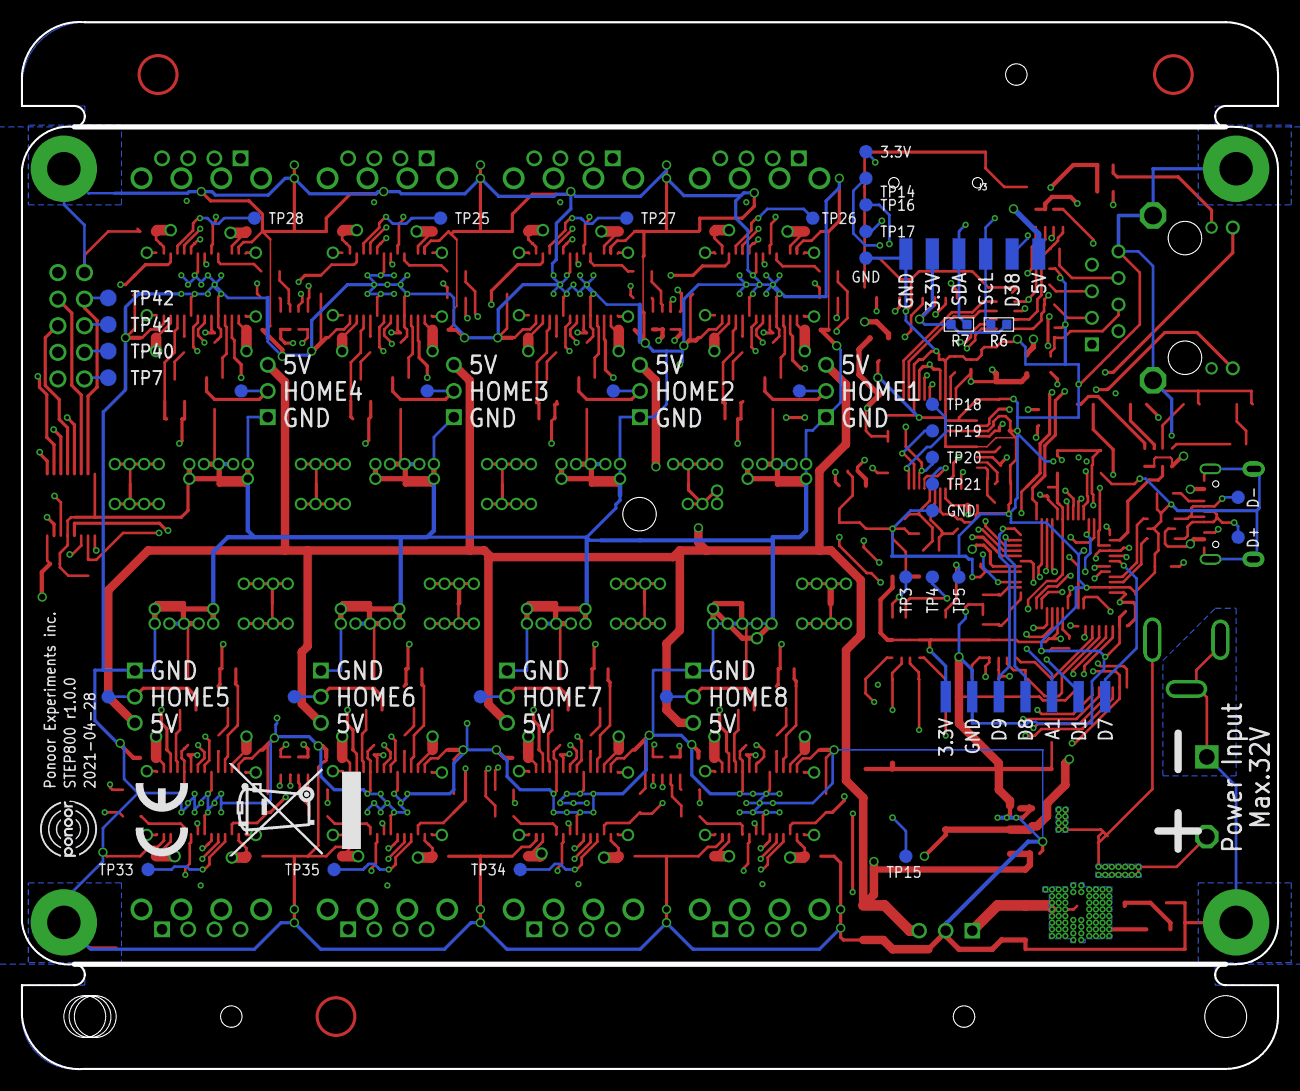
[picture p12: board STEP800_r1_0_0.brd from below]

Board: 4 copper layers, 120.0 x 100.0 mm, 280 parts (48 on the bottom side), 219 nets.

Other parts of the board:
U$1: WEEE_13MM
U$2: STEP800_LOGO_L_16MM
U$3: CE_5MM
U$4, U$5: PONOOR_LOGO_6MM

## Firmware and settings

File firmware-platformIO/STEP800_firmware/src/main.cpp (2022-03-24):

/*
 Name:		STEP800_firmware.ino

 target:    Arduino Zero
 Created:	2021/04/17 
 Author:	kanta 
*/
#include <Arduino.h>

#include "wiring_private.h" // pinPeripheral() function
#include <SPI.h>
#include <SD.h>
#include <Ethernet.h>
#include <OSCMessage.h> // https://github.com/CNMAT/OSC
#include <ArduinoJson.h> //https://arduinojson.org/
#include <Adafruit_SleepyDog.h> // https://github.com/adafruit/Adafruit_SleepyDog

#include <Ponoor_L6470Constants.h> // https://github.com/ponoor/Ponoor_L6470_Library
#include <Ponoor_L6470Library.h>

// Local files
#include "globals.h" // Global values and pin assigns
#include "utils.h"  // Utility functions
#include "oscListeners.h"   // OSC receive
#include "loadConfig.h" // Load the config file from the microSD
#include "diagnosis.h"  // USB serial diagnosis

// General
#ifdef PROTOTYPE_R3 // For prototypes. Check globals.h
const char *firmwareName = "STEP800_PROTO_R3";
#elif defined(PROTOTYPE_BLACK)
const char *firmwareName = "STEP800_PROTO_BLACK";
#else
const char *firmwareName = "STEP800_R1";
#endif
const uint8_t firmwareVersion[3] = {1,0,5};
const uint8_t applicableConfigVersion[2] = {1,2};

// L6470
#ifdef PROTOTYPE_BLACK
SPIClass L6470SPI(&sercom1, L6470_MISO, L6470_SCK, L6470_MOSI, SPI_PAD_0_SCK_1, SERCOM_RX_PAD_3);// MISO/SCK/MOSI pins
#else
SPIClass L6470SPI(&sercom3, L6470_MISO, L6470_SCK, L6470_MOSI, SPI_PAD_0_SCK_3, SERCOM_RX_PAD_2);// MISO/SCK/MOSI pins
#endif

// Servo mode
constexpr auto position_tolerance = 0; // steps

// for PlatformIO
void sendBootMsg(uint32_t _currentTime);
void resetEthernet();
void sendStatusDebug(String address, int32_t data1, int32_t data2, int32_t data3);
void checkStatus();
// void checkLimitSw();
void checkLED(uint32_t _currentTimeMillis);
void checkBrake(uint32_t _currentTimeMillis);
void updateServo(uint32_t currentTimeMicros);

void setup() {
  pinMode(ledPin, OUTPUT);
  pinMode(W5500_RESET_PIN, OUTPUT);
#ifdef HAS_SD
  pinMode(SD_CS_PIN, OUTPUT);
  pinMode(SD_DETECT_PIN, INPUT_PULLUP);
#endif
  // Stepper Driver
  boolean L6470_reset_pin_enable_state = HIGH;
#ifdef PROTOTYPE_BLACK
    L6470_reset_pin_enable_state = LOW;
#endif
  pinMode(L6470_RESET_PIN, OUTPUT);
  pinMode(L6470_CS_PIN, OUTPUT);
  pinMode(L6470_MOSI, OUTPUT);
  pinMode(L6470_MISO, INPUT);
  pinMode(L6470_SCK, OUTPUT);
  digitalWrite(L6470_RESET_PIN, L6470_reset_pin_enable_state);
  digitalWrite(L6470_RESET_PIN, !L6470_reset_pin_enable_state);
  delay(10);
  digitalWrite(L6470_RESET_PIN, L6470_reset_pin_enable_state);
  digitalWrite(L6470_CS_PIN, HIGH);
  L6470SPI.begin();
#ifdef PROTOTYPE_BLACK
  pinPeripheral(L6470_MOSI, PIO_SERCOM);
  pinPeripheral(L6470_MISO, PIO_SERCOM);
  pinPeripheral(L6470_SCK, PIO_SERCOM);
#else
  pinPeripheral(L6470_MOSI, PIO_SERCOM_ALT);
  pinPeripheral(L6470_SCK, PIO_SERCOM_ALT);
  pinPeripheral(L6470_MISO, PIO_SERCOM_ALT);
#endif
  L6470SPI.setDataMode(SPI_MODE3);

#ifdef PROTOTYPE_BLACK
    pinMode(MISO3, INPUT);
    pinMode(SCK3, OUTPUT);
    pinMode(LATCH3, OUTPUT);
    digitalWrite(LATCH3, HIGH);
#else
    // Shift Registers
	SPI3.begin();
	pinPeripheral(MISO3, PIO_SERCOM_ALT);	// MISO
	pinPeripheral(MOSI3, PIO_SERCOM);	// MOSI
	pinPeripheral(SCK3, PIO_SERCOM_ALT);		// SCK
	SPI3.beginTransaction(SPISettings(4000000, MSBFIRST, SPI_MODE0));
	pinMode(LATCH3, OUTPUT);
	digitalWrite(LATCH3, HIGH);

    #ifdef PROTOTYPE_R3
    pinMode(SETUP_SW_PIN, INPUT_PULLUP);
    #else // r1.0.0
    pinMode(SHIFTOUT_ENABLE_PIN, OUTPUT);
    digitalWrite(SHIFTOUT_ENABLE_PIN, HIGH);
    #endif
#endif

  loadConfig();

  for (uint8_t i = 0; i < NUM_OF_MOTOR; i++)
  {
      stepper[i].SPIPortConnect(&L6470SPI);
      resetMotorDriver(i + MOTOR_ID_FIRST);
      digitalWrite(ledPin, HIGH);
      delay(5);
      digitalWrite(ledPin, LOW);
      delay(5);
  }

  // Configure W5500
  digitalWrite(W5500_RESET_PIN, HIGH);
  myId = getMyId();
  delay(1);
  resetEthernet();
  isWaitingSendBootMsg = bootedMsgEnable;

  SerialUSB.begin(9600);
  Watchdog.enable(100);

  for (uint8_t i = 0; i < NUM_OF_MOTOR; i++)
  {
      if ( bHomingAtStartup[i] ) {
          homing(i);
      }
  }
  
}

void sendBootMsg(uint32_t _currentTime) {
    static uint32_t linkedTime;
    if ( Ethernet.linkStatus() == LinkOFF ) {
        linkedTime = _currentTime;
        return; 
    }
    else {
        if ((uint32_t)(_currentTime - linkedTime) < BOOT_MSG_WAIT_TIME) return;
    }
    OSCMessage newMes("/booted");
    newMes.add(myId);
    Udp.beginPacket(broadcastIp, outPort);
    newMes.send(Udp);
    Udp.endPacket();
    newMes.empty();
    turnOnTXL();
    isWaitingSendBootMsg = false;
}

void resetEthernet() {
    boolean reset_pin_enable_state = LOW;
#ifdef PROTOTYPE_BLACK
    reset_pin_enable_state = HIGH;
#endif
    digitalWrite(W5500_RESET_PIN, reset_pin_enable_state);
    digitalWrite(ledPin, HIGH);
    delay(10); // This delay is necessary to refresh the network configration.
    digitalWrite(W5500_RESET_PIN, !reset_pin_enable_state);
    digitalWrite(ledPin, LOW);
    delay(1);
    if ( isMyIpAddId ) myIp[3] = myIp_from_config[3] + myId;
    if ( isMacAddId ) mac[5] = mac_from_config[5] + myId;
    if ( isOutPortAddId ) outPort = outPort_from_config + myId;
    Ethernet.begin(mac, myIp, dns, gateway, subnet);
    Udp.begin(inPort);
    p("New IP: %d.%d.%d.%d\n", myIp[0], myIp[1], myIp[2], myIp[3]);
}

void checkStatus() {
    uint32_t t;
    for (uint8_t i = 0; i < NUM_OF_MOTOR; i++)
    {
        const auto status = stepper[i].getStatus();
        // HiZ, high for HiZ
        t = (status & STATUS_HIZ) > 0;
        if (HiZ[i] != t)
        {
            HiZ[i] = t;
            if (reportHiZ[i]) sendTwoData("/HiZ", i + MOTOR_ID_FIRST, (int32_t)t);
        }
        // BUSY, low for busy
        t = (status & STATUS_BUSY) == 0;
        if (busy[i] != t)
        {
        	busy[i] = t;
        	if ( reportBUSY[i] ) sendTwoData("/busy", i + MOTOR_ID_FIRST, (int32_t)t);
            if ( (!busy[i]) && (homingStatus[i] == HOMING_RELEASESW) ) {
                homingStatus[i] = HOMING_COMPLETED;
                if (bHoming[i]) {
                    sendTwoData("/homingStatus", i + MOTOR_ID_FIRST, homingStatus[i]);
                    bHoming[i] = false;
                }
            }
        }
        // DIR
        t = (status & STATUS_DIR) > 0;
        if (dir[i] != t)
        {
            dir[i] = t;
            if (reportDir[i]) sendTwoData("/dir", i + MOTOR_ID_FIRST, (int32_t)t);
        }
        // SW_F, low for open, high for close
        t = (status & STATUS_SW_F) > 0;
        if (homeSwState[i] != t)
        {
            homeSwState[i] = t;
            if (reportHomeSwStatus[i]) getHomeSw(i);
        }
        // SW_EVN, active high, latched
        t = (status & STATUS_SW_EVN) > 0;
        if (t) {
            if (homingStatus[i] == HOMING_GOUNTIL) {
                if (bHoming[i]) {
                    releaseSw(i, 0, !homingDirection[i]);
                    homingStatus[i] = HOMING_RELEASESW;
                    sendTwoData("/homingStatus", i + MOTOR_ID_FIRST, homingStatus[i]);
                } else {
                    homingStatus[i] = HOMING_COMPLETED;
                }
            }
            if (reportSwEvn[i]) sendOneDatum("/swEvent", i + MOTOR_ID_FIRST);
        }
        
        // MOT_STATUS
        t = (status & STATUS_MOT_STATUS) >> 5;
        if (motorStatus[i] != t) {
            motorStatus[i] = t;
            if (reportMotorStatus[i]) sendTwoData("/motorStatus", i + MOTOR_ID_FIRST, motorStatus[i]);
            if (bBrakeDecWaiting[i] && (motorStatus[i] == 0)) // motor stopped
            {
                activate(i, false);
                bBrakeDecWaiting[i] = false;
            }
        }
        // CMD_ERROR, active high, latched
        t = (status & (STATUS_WRONG_CMD | STATUS_NOTPERF_CMD) ) > 0;
        if (t) 
            sendCommandError(i + MOTOR_ID_FIRST, ERROR_COMMAND_IGNORED);
        // UVLO, active low
        t = (status & STATUS_UVLO) == 0;
        if (t != uvloStatus[i])
        {
            uvloStatus[i] = !uvloStatus[i];
            if (reportUVLO[i]) sendTwoData("/uvlo", i + MOTOR_ID_FIRST, uvloStatus[i]);
        }
        // TH_STATUS
        t = (status & (STATUS_TH_WRN|STATUS_TH_SD)) >> 10;
        t = (~t)&0x0003U;
        if (thermalStatus[i] != t) {
            thermalStatus[i] = t;
            if (reportThermalStatus[i]) sendTwoData("/thermalStatus", i + MOTOR_ID_FIRST, thermalStatus[i]);
        }
        // OCD, active low, latched
        t = (status & STATUS_OCD) == 0;
        if (t && reportOCD[i]) sendOneDatum("/overCurrent", i + 1);

        // STALL A&B, active low, latched
        t = (status & (STATUS_STEP_LOSS_A | STATUS_STEP_LOSS_B)) >> 13;
        if ((t != 3) && reportStall[i]) sendOneDatum("/stall", i + MOTOR_ID_FIRST);
    }
}

void checkLED(uint32_t _currentTimeMillis) {
    if (rxLedEnabled)
    {
        if ((uint32_t)(_currentTimeMillis - RXL_blinkStartTime) >= RXL_TXL_BLINK_DURATION)
        {
            rxLedEnabled = false;
            digitalWrite(PIN_LED_RXL, HIGH); // turn off
        }
    }
    if (txLedEnabled)
    {
        if ((uint32_t)(_currentTimeMillis - TXL_blinkStartTime) >= RXL_TXL_BLINK_DURATION)
        {
            txLedEnabled = false;
            digitalWrite(PIN_LED_TXL, HIGH); // turn off
        }
    }
}

void checkBrake(uint32_t _currentTimeMillis) {
    for (uint8_t i = 0; i < NUM_OF_MOTOR; i++)
    {
        if (electromagnetBrakeEnable[i]) {
            if (brakeStatus[i] == BRAKE_DISENGAGE_WAITING) {
                if ((uint32_t)(_currentTimeMillis - brakeTransitionTrigTime[i]) >= brakeTransitionDuration[i]) {
                    #ifdef HAS_BRAKE
                    setBrake(i, HIGH);
                    #endif
                    brakeStatus[i] = BRAKE_DISENGAGED;
                }
            } else if (brakeStatus[i] == BRAKE_MOTORHIZ_WAITING) {
                if ((uint32_t)(_currentTimeMillis - brakeTransitionTrigTime[i]) >= brakeTransitionDuration[i]) {
                    stepper[i].hardHiZ();
                    brakeStatus[i] = BRAKE_ENGAGED;
                }
            }
        }
    }
    
}

void checkHomingTimeout(uint32_t _currentTimeMillis) {
    for (uint8_t i = 0; i < NUM_OF_MOTOR; i++) {
        if ((homingStatus[i] == HOMING_GOUNTIL) && (goUntilTimeout[i] > 0)) {
            if ((uint32_t)(_currentTimeMillis - homingStartTime[i]) >= goUntilTimeout[i]) {
                stepper[i].hardStop();
                sendCommandError(i + MOTOR_ID_FIRST, ERROR_GOUNTIL_TIMEOUT);
                homingStatus[i] = HOMING_TIMEOUT;
                if (bHoming[i]) {
                    sendTwoData("/homingStatus", i + MOTOR_ID_FIRST, homingStatus[i]);
                    bHoming[i] = false;
                }
            }
        } 
        else if ((homingStatus[i] == HOMING_RELEASESW) && (releaseSwTimeout[i] > 0)) {
            if ((uint32_t)(_currentTimeMillis - homingStartTime[i]) >= releaseSwTimeout[i]) {
                stepper[i].hardStop();
                sendCommandError(i + MOTOR_ID_FIRST, ERROR_RELEASESW_TIMEOUT);
                homingStatus[i] = HOMING_TIMEOUT;
                    if (bHoming[i]) {
                        sendTwoData("/homingStatus", i + MOTOR_ID_FIRST, homingStatus[i]);
                    bHoming[i] = false;
                }
            }

        }
    }
}

void updatePositionReport(uint32_t _currentTimeMillis) {
    static uint32_t lastPollTime[NUM_OF_MOTOR] = { 0,0,0,0 };
    for (uint8_t i=0; i<NUM_OF_MOTOR; i++) {
        if (reportPosition[i]) {
            if ((uint32_t)(_currentTimeMillis - lastPollTime[i]) >= reportPositionInterval[i]) {
                sendTwoData("/position", i + MOTOR_ID_FIRST, stepper[i].getPos());
                lastPollTime[i] = _currentTimeMillis;
            }
        }
    }
}

void updatePositionReportList(uint32_t _currentTimeMillis) {
    static uint32_t lastPollTime = 0;
    if ((uint32_t)(_currentTimeMillis - lastPollTime) >= reportPositionListInterval) {
        getPositionList();
        lastPollTime = _currentTimeMillis;
    }
}

void updateServo(uint32_t currentTimeMicros) {
    static uint32_t lastServoUpdateTime = 0;
    static float eZ1[NUM_OF_MOTOR] = { 0,0,0,0 },
        // eZ2[NUM_OF_MOTOR] = { 0,0,0,0 },
        integral[NUM_OF_MOTOR] = { 0,0,0,0 };
    float spd = 0.0;
    if ((uint32_t)(currentTimeMicros - lastServoUpdateTime) >= 100) {
        for (uint8_t i = 0; i < NUM_OF_MOTOR; i++) {
            if (isServoMode[i]) {
                int32_t error = targetPosition[i] - stepper[i].getPos();
                integral[i] += ((error + eZ1[i]) / 2.0f);
                if (integral[i] > 1500.0f) integral[i] = 1500.0f;
                else if (integral[i] < -1500.0f) integral[i] = -1500.0f;
                if (fabsf(error) > position_tolerance) {
                    double diff = error - eZ1[i];

                    spd = error * kP[i] + integral[i] * kI[i] + diff * kD[i];
                }
                // eZ2[i] = eZ1[i];
                eZ1[i] = error;
                float absSpd = fabsf(spd);
                //if (absSpd < 1.0f) {
                //    spd = 0.0;
                //}
                stepper[i].run((spd > 0.0f), absSpd);
            }
        }
        lastServoUpdateTime = currentTimeMicros;
    }
}

void loop() {
    uint32_t 
        currentTimeMillis = millis(),
        currentTimeMicros = micros();
    static uint32_t lastPollTime = 0;

    if ((uint32_t)(currentTimeMillis - lastPollTime) >= STATUS_POLL_PERIOD)
    {
        //checkLimitSw();
#ifdef HAS_BRAKE
        checkBrake(currentTimeMillis);
#endif
        checkHomingTimeout(currentTimeMillis);
        updatePositionReport(currentTimeMillis);
        if ( reportPositionList) 
            updatePositionReportList(currentTimeMillis);
        checkStatus();
        checkLED(currentTimeMillis);
        uint8_t t = getMyId();
        if (myId != t) {
            myId = t;
            resetEthernet();
        }
        Watchdog.reset();
        lastPollTime = currentTimeMillis;
    }

    if (SerialUSB.available() > 0)
    {
        diagnosisCommand(SerialUSB.read());
    }
    if (isWaitingSendBootMsg) { sendBootMsg(currentTimeMillis); }
    OSCMsgReceive();
    updateServo(currentTimeMicros);
}

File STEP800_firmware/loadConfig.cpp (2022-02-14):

// 
// 
// 
#include "loadConfig.h"

void loadConfig() {
    uint8_t i;
    #ifdef PROTOTYPE_BLACK
    sdInitializeSucceeded = false;
    configFileOpenSucceeded = false;
    configFileParseSucceeded = false;
    DynamicJsonDocument doc(8192);
    #else
    if (digitalRead(SD_DETECT_PIN) == LOW)
    {
        sdInitializeSucceeded = SD.begin(SD_CS_PIN);
    }
    File file = SD.open(filename);
    configFileOpenSucceeded = (file != false);
    // Allocate a temporary JsonDocument
    // Don't forget to change the capacity to match your requirements.
    // Use arduinojson.org/v6/assistant to compute the capacity.
    DynamicJsonDocument doc(8192);
    DeserializationError error = deserializeJson(doc, file);
    if (error) {
        p("Failed to read file: %s\nUsing default configuration.\n", error.f_str());
    }
    configFileParseSucceeded = (error == DeserializationError::Ok);
    file.close();
    SD.end();
    #endif

    // Information
    JsonObject information = doc["information"];
    configName = information["configName"] | "Default";
    if (configFileOpenSucceeded) {
        for (i=0;i<2; i++) {
            loadedConfigVersion[i] = information["configVersion"][i] | 0;
        }
    }
    configTargetProduct = information["targetProduct"] | "---";
    configProductApplicable = (configTargetProduct == productName);

    // Network
    JsonObject network = doc["network"];
    JsonArray network_myIp = network["myIp"];
    JsonArray network_destIp = network["destIp"];
    JsonArray network_dns = network["dns"];
    JsonArray network_gateway = network["gateway"];
    JsonArray network_subnet = network["subnet"];
    for (i = 0; i < 4; i++) {
        myIp[i] = network_myIp[i] | myIp[i];
        myIp_from_config[i] = myIp[i];
        destIp[i] = network_destIp[i] | destIp[i];
        dns[i] = network_dns[i] | dns[i];
        gateway[i] = network_gateway[i] | gateway[i];
        subnet[i] = network_subnet[i] | subnet[i];
    }
    isMyIpAddId = (int)network["isMyIpAddId"] | true;
    inPort = network["inPort"] | 50000;
    outPort = network["outPort"] | 50100;
    outPort_from_config = outPort;
    isOutPortAddId = (int)network["isOutPortAddId"] | true;
    JsonArray network_mac = network["mac"];
    for (i = 0; i < 6; i++) {
        mac[i] = network_mac[i] | mac[i];
        mac_from_config[i] = mac[i];
    }
    isMacAddId = (int)network["isMacAddId"] | true;
    bootedMsgEnable = (int)network["bootedMsgEnable"] | true;
    isDestIpSet = (int)network["canSendMsgBeforeDestIp"] | false;
    reportErrors = (int)network["reportError"] | true;
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

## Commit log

2021-04-14 Added hardware design files
    [STEP800_r1_0_0.brd, STEP800_r1_0_0.sch]
2021-04-23 Added multiple boards support
2021-04-27 Fixed a SPI pin for shift registers
    [globals.cpp, globals.h, main.cpp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]
2021-04-28 Fixed loading myIp, outPort and mac when the DIP sw changed.
    And PROTOTYPE_BLACK bugs fix
    [globals.cpp, globals.h, loadConfig.cpp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]
2021-04-28 Updated hardware design files
    [STEP800_r1.0.0 BOM.xlsx, STEP800_r1_0_0.brd, STEP800_r1_0_0.sch]
2021-04-30 Fixed the L6470 reset pin logic state for prototype pcb
    [loadConfig.cpp, main.cpp]
2021-05-03 Fixed the wrong parsing when loading integer as bool in the config.txt
    [loadConfig.cpp]
2021-05-07 Silk adjustments for the Eagle board design file
    [STEP800_r1.0.0_BOM.csv, STEP800_r1_0_0.brd]
2021-05-17 Correct the external OSC frequency for prototype_black
    [utils.cpp]
2021-08-30 configTools item name typo fixed
    goUntilTimeout
    [Ponoor_L6470Commands.cpp, Ponoor_L6470Config.cpp, Ponoor_L6470Library.cpp]
2021-09-03 Fixed the diagnosis tool serial output problem
    [diagnosis.cpp]
2021-09-03 Fixed a usb serial output problem of the diagnosis tool
    [STEP800_firmware.ino, diagnosis.cpp, main.cpp]
2021-09-13 led test sketch
2021-09-14 led test sketch update
2021-10-18 Update Arduino sketch folder
2021-12-02 added /resetDeive and remove /resetDev
    [oscListeners.cpp]
2021-12-08 updated Arduino sketch folder
2022-01-14 fixed `/getLowSpeedOptimizeThreshold` response bug.
    [STEP800_firmware.ino, main.cpp, oscListeners.cpp]
2022-01-19 Fixed the thermal status return value
    [STEP800_firmware.ino, main.cpp]
2022-02-13 check the homing status for motion/stop commands
2022-02-14 only `/run` can interrupt a homing among motion commands
    Other motion commands will be ignored during a homing.
2022-03-03 Fixed the incorrect `/getHomeSw` response.
    [main.cpp, oscListeners.cpp]
2023-03-10 generate the brake board schematic
    [STEP800_brakeConverter.kicad_pcb, STEP800_brakeConverter.kicad_sch]
2023-03-10 generate the board layout
    [STEP800_brakeConverter.kicad_pcb, STEP800_brakeConverter.kicad_sch]
2023-03-17 brake board pcb design update
    [STEP800_brakeConverter.kicad_pcb]
2023-04-05 brake conv gerber data for the prototype
    [STEP800_brakeConverter-B_Cu.gbr, STEP800_brakeConverter-B_Mask.gbr, STEP800_brakeConverter-B_Paste.gbr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]
2023-09-09 hardware test sketch update to adapt new SAMD SPI function name
2023-09-10 The hardware test sketch updated
    Added LED tests.

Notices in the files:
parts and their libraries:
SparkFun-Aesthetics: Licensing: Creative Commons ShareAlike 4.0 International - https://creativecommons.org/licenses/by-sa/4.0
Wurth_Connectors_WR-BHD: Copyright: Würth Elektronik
